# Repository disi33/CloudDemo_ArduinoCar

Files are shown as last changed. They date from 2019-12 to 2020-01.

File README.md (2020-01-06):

## Important note:

If you're running into the following error while compiling, refer to the section [Notes on the implementation](https://github.com/disi33/CloudDemo_ArduinoCar/blob/master/README.md#notes-on-the-implementation) on how to resolve it:

```
lto1.exe: internal compiler error: in lto_output_varpool_node
```

# Table of contents

* [Repository contents](https://github.com/disi33/CloudDemo_ArduinoCar/blob/master/README.md#repository-contents)

* [Hardware and accessories](https://github.com/disi33/CloudDemo_ArduinoCar/blob/master/README.md#hardware-and-accessories)
  - [Hardware](https://github.com/disi33/CloudDemo_ArduinoCar/blob/master/README.md#hardware)
  - [Accessories](https://github.com/disi33/CloudDemo_ArduinoCar/blob/master/README.md#accessories)
  
* [Modules](https://github.com/disi33/CloudDemo_ArduinoCar/blob/master/README.md#modules)
  * [GPS Module](https://github.com/disi33/CloudDemo_ArduinoCar/blob/master/README.md#gps-module)
  * [ESP8266 (WiFi module)](https://github.com/disi33/CloudDemo_ArduinoCar/blob/master/README.md#esp8266-wifi-module)
    * [Notes on ESP8266](https://github.com/disi33/CloudDemo_ArduinoCar/blob/master/README.md#notes-on-esp8266)
    * [Additional notes](https://github.com/disi33/CloudDemo_ArduinoCar/blob/master/README.md#additional-notes)
  * [Wireless XBOX 360 adapter](https://github.com/disi33/CloudDemo_ArduinoCar/blob/master/README.md#wireless-xbox-360-adapter)
  
* [Software](https://github.com/disi33/CloudDemo_ArduinoCar/blob/master/README.md#software)
  - [Libraries](https://github.com/disi33/CloudDemo_ArduinoCar/blob/master/README.md#libraries)
  - [Enabling and disabling modules](https://github.com/disi33/CloudDemo_ArduinoCar/blob/master/README.md#enabling-and-disabling-modules)
  - [Notes on the implementation](https://github.com/disi33/CloudDemo_ArduinoCar/blob/master/README.md#notes-on-the-implementation)

# Repository contents

This repository contains:
- The source code of the program run on the car, written in the [Arduino IDE](https://www.arduino.cc/en/main/software)
- Schematics and reference pictures of the power-regulated WiFi module and the final build of the car
  * The schematics are made with [fritzing](http://fritzing.org/home/). You can use fritzing to open the .fzz file and edit the schematics or use it to create a proper PCB.
- A list of hardware and accessories used to finish this project

# Hardware and accessories

## Hardware
- The base [RC car kit](https://www.amazon.com/VKmaker-Avoidance-tracking-Ultrasonic-tutorial/dp/B01CXVA6IO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).
- An [Arduino USB host shield](https://www.amazon.com/gp/product/B006J4G000/ref=ppx_yo_dt_b_search_asin_title?ie=UTF8&psc=1) for USB capabilities to enable XBOX controllers.
- An [Arduino Sensor shield](https://www.amazon.com/KNACRO-Sensor-Expansion-Arduino-Genuino/dp/B01N2OLLH0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) for better access to pins and easier wiring.
- An [XBOX 360 wireless controller](https://www.amazon.com/gp/product/B073WJCQGT/ref=ppx_yo_dt_b_search_asin_title?ie=UTF8&th=1) and [receiver](https://www.amazon.com/gp/product/B00TGL39TI/ref=ppx_yo_dt_b_search_asin_title?ie=UTF8&psc=1).
- A [GPS module](https://www.amazon.com/gp/product/B01AW5QYES/ref=ppx_yo_dt_b_search_asin_title?ie=UTF8&psc=1).
- An [ESP8266 ESP-01 WiFi module](https://www.amazon.com/MakerFocus-Wireless-Transceiver-DC3-0-3-6V-Compatible/dp/B01EA3UJJ4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)
- A [3.3V Step Down Power Supply Voltage Regulator](https://www.amazon.com/gp/product/B01N1I1LXH/ref=ppx_yo_dt_b_search_asin_title?ie=UTF8&psc=1) module.
- A roughly [3x7cm prototype board](https://www.amazon.com/uxcell-Universal-Printed-Circuit-Soldering/dp/B07FK47K22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) as a base for the power-regulated WiFi module.
- A [400 pin breadboard](https://www.amazon.com/gp/product/B077DN2PS1/ref=ppx_yo_dt_b_asin_title_o02_s00?ie=UTF8&psc=1) to fit the extra components neatly above the battry pack in the back of the car.
- A reasonable assortments of electronic parts (resistors: 1k, 2k, 10k; capacitors: 0.22uF, 470uF; jumper cables; [male and female pin header connector rows](https://www.amazon.com/Pieces-Female-Connector-Straight-Arduino/dp/B07VNXL5BD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))

## Accessories

- soldering kit
- AA batteries for the car and the XBOX 360 controller
- [USB Serial module for the ESP8266](https://www.amazon.com/gp/product/B07KF119YB/ref=ppx_yo_dt_b_asin_title_o00_s00?ie=UTF8&psc=1)
- tape for fixing the breadboard and the wireless controller adapter to the car
- optional: rubber bands (the tires in some car kits do not create enough friction on most surfaces, you can put rubber bands around them to increase traction)

# Modules

## GPS Module

The GPS module is connected as follows:

| GPS | - | Arduino |
|-----|-----|---|
| VCC | <-> | +5V |
| GND | <-> | GND |
| TxD | <-> | PIN 18 (A4) |
| RxD | <-> | PIN 19 (A5) |

## ESP8266 (WiFi module)

**ATTENTION:** The ESP8266 operates on 3.3V, while the Arduino operates on 5V! Do not connect the ESP8266 to 5V, use a step down regulator to convert the Voltage. The ESP8266 may not function correctly or even break/brick if operated under 5V. For the same reasons, use a 1k and a 2k resistor to step down the signal coming from the arduino on the ESP8266's RxD line!

The ESP8266 is generally connected as follows:

| ESP8266 | - | Arduino |
|---|-----|---|
| VCC | <-> | +3.3V (generated from step down regulator) |
| GND | <-> | GND |
| TxD | <-> | PIN 4 |
| RxD | <-> | PIN 3 (through step down resistors) |
| CH_PD | <-> | +3.3V (through 10k pull-up resistor) |

### Notes on ESP8266:

When idle, the ESP8266 draws about 30-50 mA, but during peak load draws of about 300mA are not unseen. I recommend to use stabilizer capacitors of 470uF near the step down regulator and 0.22uF near the ESP8266 to help with sudden spikes. The capacitors should be as near as possible to their respective counterpart parts, since too much resistance on the cables running up to them can negate their intended functionality.

So all-in-all the ESP8266 requires quite a bit of extra work here:
- step down power source voltage from 5V to 3.3V
- add additional step down resistors for incoming signals from Arduino
- a pull up resistor for CH_PD
- stabilizing capacitors for smoother power supply during peak load times

The breadboard can be very restrictive in space and in how to place these components, so I recommend creating this circuit as a separate module on a prototype board. When doing so, please keep these things in mind:
- You can solder a piece of a male connector row to the bottom of the connector board, that way you can put the module into the breadboard vertically.
- Ensure the capacitors are placed close to the step down regulator and the ESP8266 respectively.
- You can use 2 4-pieces of female connector rows as a base for the ESP8266 to sit in. That way you can easily remove it for programming purposes or replace it when broken.

### Additional notes:

Most ESP8266 come pre-programmed to a baud rate of 115200. Arduinos regularly struggle to communicate at such a baud rate over Serial buses and it is recommended to user a lower baud rate. Use a USB interface to manually set the baud rate of the ESP8266 to 9600. (All source code distributed in this repo assumes a baud rate of 9600.)

A power supply of 6 AA-batteries should mostly be sufficient to operate the ESP8266 in addition to all other components on the car. That being said, I have experienced situation where the ESP8266 was suddenly becoming unresponsive. I suspect this is due to the power supply not being able to supply high enough current during peak workload, so I recommend not spamming the module with HTTP requests and limiting the use to 1 request every few seconds to minimize the need for resets.

## Wireless XBOX 360 adapter

Use the USB shield to connect the USB adapter to the Arduino. You can run the cable underneath the base plate of the car and use tape to fix the cable and the receiver to the bottom of the plate.

# Software

Use the [Arduino IDE](https://www.arduino.cc/en/Main/Software) to upload the program onto the Arduino and to read the output on the Serial connection via the IDE's Serial Monitor.

## Libraries

This project is using:
- the [USB Host Shield Library 2.0](https://github.com/felis/USB_Host_Shield_2.0) to connect to the XBOX Controller via the wireless adapter.
- the [ESP8266_Simple library](https://github.com/sleemanj/ESP8266_Simple) to operate the ESP8266 module.

## Enabling and disabling modules

The program consists of 3 basic modules that can be enabled and disabled before uploading the program to the Arduino:
- **Controller:** for remote controlling the car using an XBOX 360 controller
- **GPS:** for reading the car's GPS location
- **WiFi:** for spinning up a HTTP server on the car to interact with it over WiFi

You can enable and disable these modules on top of the program file. When enabling the WiFi module, you must also specify the SSID and password of the WiFi network to connect to.

## Notes on the implementation

- Both the USB Host Shield library and the ESP8266_Simple library are using the [SoftwareSerial library](https://www.arduino.cc/en/Reference/SoftwareSerial) to communicate with their respective modules. Unfortunately, while SoftwareSerial allows for specifying several Serial connections on different pins, as of now this library only allows for **only one Serial port to be operated at a time**. Especially the ESP8266_Simple library seems to struggle to maintain its internal state when a different SoftwareSerial port is being operated. Enabling this functionality would require a complete overhaul of the used libraries. To work around this, for now the GPS data is only read from the GPS module once before the ESP8266_Simple Serial connection is established.
- At the time of writing this, some of the used libraries are incompatible with the latest version of the **Arduino AVR Boards** board libraries used by the Arduino IDE. When running into issues while compiling or uploading the program, try downgrading the library version to version **1.6.20** in the IDE's board manager (Tools -> Board: "<Board Name>" -> Board Manager...).
- The controller module allows for remote controlling the cars movement using the D-Pad. The current implementation is very basic and might occasionally drop an input, but should be sufficient for demo purposes.
- The program is writing quite some information to the default Serial connection. You can use the Arduino IDE's Serial Monitor to debug the program if the car shows unexpected behavior. Note that the demo software used to display the car's IP address after establishing WiFi connection on the serial port, but due to some incompatibilities between the latest ESP8266 firmware and the latest Arduino libraries, we cannot easily do that right now. I recommend setting up the demo using a phone hotspot and reading the IP address from your phone as a fast way to get a connection and knowing the car's IP address.

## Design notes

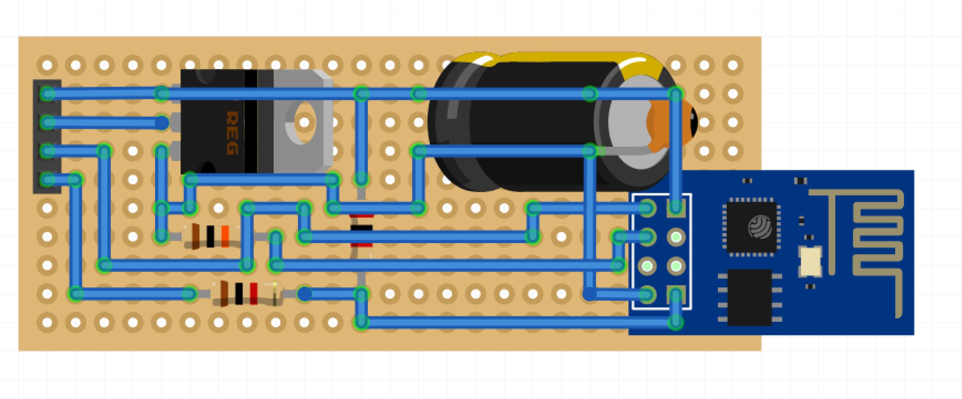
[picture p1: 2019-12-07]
schematics/breadboard_layout.PNG

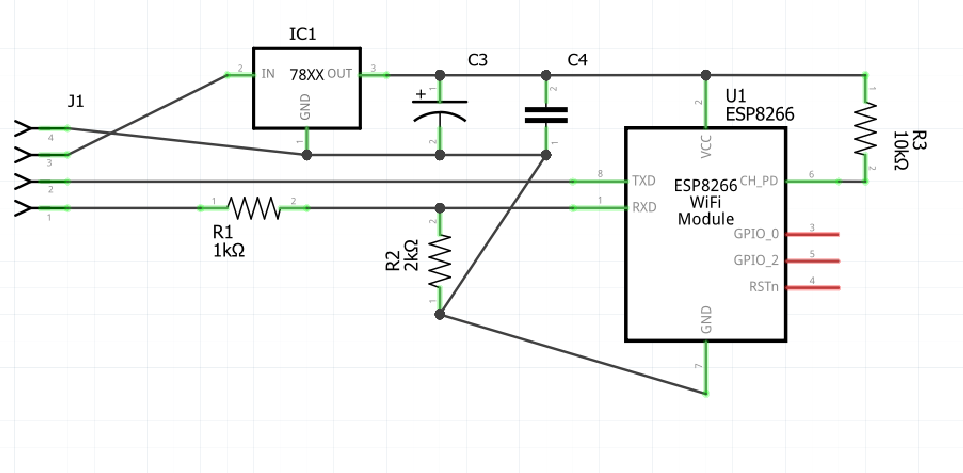
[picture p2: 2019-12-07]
schematics/schematic.PNG

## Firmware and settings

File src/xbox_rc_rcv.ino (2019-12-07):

#include <ESP8266_Simple.h>
#include <SoftwareSerial.h>
#include <XBOXRECV.h>
#include <SPI.h>
#include <Servo.h>

#if 0
  #define INCLUDE_CONTROLLER
#endif

#if 1
  #define INCLUDE_GPS
#endif

#if 1
  #define INCLUDE_WIFI
  // These are the SSID and PASSWORD to connect to your Wifi Network
  //  put details appropriate for your network between the quote marks,
  //  eg  #define ESP8266_SSID "YOUR_SSID"
  #define ESP8266_SSID  "UnwiredHome"
  #define ESP8266_PASS  "L3nticular"
#endif

#ifdef INCLUDE_CONTROLLER
// XBox Controller members
USB Usb;
XBOXRECV Xbox(&Usb);

// internal state members
enum DIRECTION {
  STRAIGHT,
  BACKWARDS,
  GOLEFT,
  GORIGHT,
  STOP
};

int pinLB=17;     // Define a 14 Pin
int pinLF=14;     // Define a 15 Pin
int pinRB=15;    // Define a 16 Pin
int pinRF=16;    // Define a 17 Pin
DIRECTION currentDirection = STOP;

void go()     // go
{
  //Serial.println("straight");
  digitalWrite(pinRF,HIGH);  // 16 feet for high level
  digitalWrite(pinRB,LOW);   //17 feet for low level
  //analogWrite(MotorRPWM,180);//Set the output speed(PWM)
  digitalWrite(pinLF,HIGH);  // 14 feet for high level
  digitalWrite(pinLB,LOW);   //15 feet for high level
  //analogWrite(MotorLPWM,180);//Set the output speed(PWM)
}

void right()        //right
{
  //Serial.println("go_right");
  digitalWrite(pinRB,LOW);   
  digitalWrite(pinRF,HIGH);
  //analogWrite(MotorRPWM,250);
  digitalWrite(pinLB,LOW);
  digitalWrite(pinLF,LOW);
}
    
void left()         //left
{
  //Serial.println("go_left");
  digitalWrite(pinRB,LOW);
  digitalWrite(pinRF,LOW);
  digitalWrite(pinLB,LOW);   
  digitalWrite(pinLF,HIGH);
  //analogWrite(MotorLPWM,250);
}
    
void stopp()         //stop
{
  //Serial.println("stop");
  digitalWrite(pinRB,LOW);
  digitalWrite(pinRF,LOW);
  digitalWrite(pinLB,LOW);
  digitalWrite(pinLF,LOW);
}

void back()          //back
{
  //Serial.println("back");
  digitalWrite(pinRF,LOW);  
  digitalWrite(pinRB,HIGH);
  //analogWrite(MotorRPWM,0);
  digitalWrite(pinLF,LOW);  
  digitalWrite(pinLB,HIGH);
  //analogWrite(MotorLPWM,230);
}

void move(DIRECTION dir) {
  switch(dir) {
    case STRAIGHT:
      go();
      break;
    case BACKWARDS:
      back();
      break;
    case GOLEFT:
      left();
      break;
    case GORIGHT:
      right();
      break;
    case STOP:
    default:
      stopp();
      break;
  }
}
#endif

// we use longitude/latitude outside the GPS context too, so define globally.
String RMClatitude,RMClongitude;
#ifdef INCLUDE_GPS
// GPS members
String data="";
int mark = 0;
boolean Mark_Start=false;
boolean valid=false;
String GGAUTCtime,GGAlatitude,GGAlongitude,GPStatus,SatelliteNum,HDOPfactor,Height,
PositionValid,RMCUTCtime,Speed,Direction,Date,Declination,Mode;
SoftwareSerial SerialGPS(18, 19); // use pin 18 & 19 as Rx and Tx

// GPS helper methods
String reader(){
  String value="";
  int temp;
startover:
  while (SerialGPS.available() > 0){
    delay(2);
    temp=SerialGPS.read();
    if((temp==',')||(temp=='*')){
      if(value.length()){
        return value;
      }
      else {
        return "";
      }     
    }
    else if(temp=='$'){
      // failure
      Mark_Start=false;
    }
    else{
      value+=char(temp);
    }
  }
  while (!(SerialGPS.available()>0)){
  }
  goto startover;
}
#endif

#ifdef INCLUDE_WIFI
ESP8266_Simple wifi(4,3);

unsigned long httpCommand(char *buffer, int bufferLength)
{  
  Serial.println("Evoked /command handler.");
  static int cnt = 0;
  
  cnt++;
  String numberString = String(cnt);

  memset(buffer,0,bufferLength);
  strncpy_P(buffer, numberString.c_str(), bufferLength-strlen(buffer));
  
  // And return the type and HTTP response code combined with "|" (bitwise or)
  // Valid  types are: ESP8266_HTML, ESP8266_TEXT, ESP8266_RAW
  // Valid  response codes are: any standard HTTP response code (typically, 200 for OK, 404 for not found, and 500 for error)
  
  return ESP8266_HTML | 200;
}

unsigned long http404(char *buffer, int bufferLength)
{  
  Serial.println("Evoked 404 handler.");
  memset(buffer, 0, bufferLength);  
  strcpy_P(buffer, PSTR("<h1>Error, Unknown Command</h1>\r\n<p>Try <a href=\"/command\">/command</a>.</p>"));
  return ESP8266_HTML | 404;
}

unsigned long httpGPS(char *buffer, int bufferLength)
{  
  Serial.println("Evoked GPS handler.");
  memset(buffer, 0, bufferLength);
  strncpy_P(buffer, PSTR("{\"latitude\": \""), bufferLength);
  strncpy(buffer+strlen(buffer), RMClatitude.c_str(), bufferLength-strlen(buffer));
  strncpy_P(buffer+strlen(buffer), PSTR("\", \"longitude\": \""), bufferLength-strlen(buffer));
  strncpy(buffer+strlen(buffer), RMClongitude.c_str(), bufferLength-strlen(buffer));
  strncpy_P(buffer+strlen(buffer), PSTR("\"}"), bufferLength-strlen(buffer));
  Serial.println("Send GPS response");
  Serial.print("Longitude: ");
  Serial.println(RMClongitude);
  Serial.print("Latitude: ");
  Serial.println(RMClatitude);
  return ESP8266_HTML | 200;
}
#endif

void setup()
{
  Serial.begin(9600); // Serial Port - USB connection to PC for debugging

#ifdef INCLUDE_GPS
  Serial.println("Begin GPS setup");
  SerialGPS.begin(9600); // 9600 is the baud rate
  Serial.println("GPS setup finished!");

  Serial.println("Read GPS data");
  bool dataRead = false;
  do {
    // get GPS data
    SerialGPS.listen();
    delay(2);
    while(SerialGPS.available() > 0) {    
      Serial.println("GPS available");
      if(Mark_Start){
        data=reader();
        //Serial.println(data);
        if(data.equals("GPGGA")){
          //Serial.println(1);
          GGAUTCtime=reader();
          GGAlatitude=reader();
          GGAlatitude+=reader();
          GGAlongitude=reader();
          GGAlongitude+=reader();
          GPStatus=reader();
          SatelliteNum=reader();
          HDOPfactor=reader();
          Height=reader();
          Mark_Start=false;
          valid=true;
          data="";
  
        }
        else if(data.equals("GPGSA")){\
          Mark_Start=false;
          data="";
        }
        else if(data.equals("GPGSV")){\
          Mark_Start=false;
          data="";
        }
        else if(data.equals("GPRMC")){\
          RMCUTCtime=reader();
          PositionValid=reader();
          RMClatitude=reader();
          RMClatitude+=reader();
          RMClongitude=reader();
          RMClongitude+=reader();
          Speed=reader();
          Direction=reader();
          Date=reader();
          Declination=reader();
          Declination+=reader();
          Mode=reader();
          valid=true;
          Mark_Start=false;
          data="";
        }
        else if(data.equals("GPVTG")){\
          Mark_Start=false;
          data="";
        }
        else{\
          Mark_Start=false;
          data="";
          break;
        }
      }
      if(valid){
        if(PositionValid!="A"){
          Serial.println("Your position is not valid.");
        }
        Serial.print("Date:");
        Serial.println(Date);
        Serial.print("UTCtime:");
        Serial.print(RMCUTCtime);
        Serial.print("   ");
        Serial.println(GGAUTCtime);
        Serial.print("Latitude:");
        Serial.print(RMClatitude);
        Serial.print("   ");
        Serial.println(GGAlatitude);
        Serial.print("Longitude:");
        Serial.print(RMClongitude);
        Serial.print("   ");
        Serial.println(GGAlongitude);
        Serial.print("GPStatus:");
        Serial.println(GPStatus);
        Serial.print("SatelliteNum:");
        Serial.println(SatelliteNum);
        Serial.print("HDOPfactor:");
        Serial.println(HDOPfactor);
        Serial.print("Height:");
        Serial.println(Height);
        Serial.print("Speed:");
        Serial.println(Speed);
        Serial.print("Direction:");
        Serial.println(Direction);
        Serial.print("Declination:");
        Serial.println(Declination);
        Serial.print("Mode:");
        Serial.println(Mode);   
        valid=false;
        dataRead=true;
        break;
      }
      if(SerialGPS.find("$")){
        Mark_Start=true;
      }
    }
  }
  while(!dataRead);
#endif   

#if defined INCLUDE_WIFI && defined INCLUDE_GPS
// stop GPS serial if we also have WiFi, so they don't interfere
Serial.println("Stop GPS serial.");
SerialGPS.end();
#endif

// WiFi has to be initialized after GPS, since we cannot lose listen status on the WiFi Serial Port!                                                                                                                                                                                                                                                                                                                                                                                                                                                                                                                                                                       
#ifdef INCLUDE_WIFI
  Serial.println("Begin WiFi setup");

  static ESP8266_HttpServerHandler myServerHandlers[] = {
    { PSTR("GET /command"), httpCommand },
    { PSTR("GET /gps"), httpGPS },
    { PSTR("GET "), http404 }
  };
  
  wifi.begin(9600); // Serial Port - WiFi module
  wifi.setupAsWifiStation(ESP8266_SSID, ESP8266_PASS, &Serial);
  wifi.startHttpServer(80, myServerHandlers, sizeof(myServerHandlers), 250, &Serial);
  Serial.println("WiFi setup finished!");
#endif

#ifdef INCLUDE_CONTROLLER
  // Setup motor pins
  pinMode(pinLB, OUTPUT); // Define 14 pin for the output (PWM)
  pinMode(pinLF, OUTPUT); // Define 15 pin for the output (PWM)
  pinMode(pinRB, OUTPUT); // Define 16 pin for the output (PWM) 
  pinMode(pinRF, OUTPUT); // Define 17 pin for the output (PWM)
  if (Usb.Init() == -1) {
    while (1); //halt
  }
#endif
}

void loop() 
{
#ifdef INCLUDE_WIFI
  wifi.serveHttpRequest();
#endif

#ifdef INCLUDE_CONTROLLER
  Usb.Task();
  if (Xbox.XboxReceiverConnected) {
    for (uint8_t i = 0; i < 4; i++) {
      if (Xbox.Xbox360Connected[i]) {
        currentDirection = STOP;

        if (Xbox.getButtonPress(UP, i)) {
          currentDirection = STRAIGHT;
        }
        if (Xbox.getButtonPress(DOWN, i)) {
          currentDirection = BACKWARDS;
        }
        if (Xbox.getButtonPress(LEFT, i) && currentDirection != BACKWARDS) {
          currentDirection = GOLEFT;
        }
        if (Xbox.getButtonPress(RIGHT, i) && currentDirection != BACKWARDS) {
          currentDirection = GORIGHT;
        }
        
        if (Xbox.getButtonClick(SYNC, i)) {
          Xbox.disconnect(i);
        }
      }
    }
  }
  else {
    Serial.println("No Xbox controller connected!");
  }

  move(currentDirection);
#endif
}
